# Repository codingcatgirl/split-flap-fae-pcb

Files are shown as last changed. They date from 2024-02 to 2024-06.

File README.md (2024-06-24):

# Split-Flap Fae PCB

This repository contains an alternative, improved, (near) drop-in replacement PCB for [David Kingsman's Split-Flap Display](https://github.com/Dave19171/split-flap). 

**Please note** that due to some changes in pinout, you need to use [evilscientress' improved fork of the firmware](https://github.com/evilscientress/split-flap), which was specifically created along with this PCB.

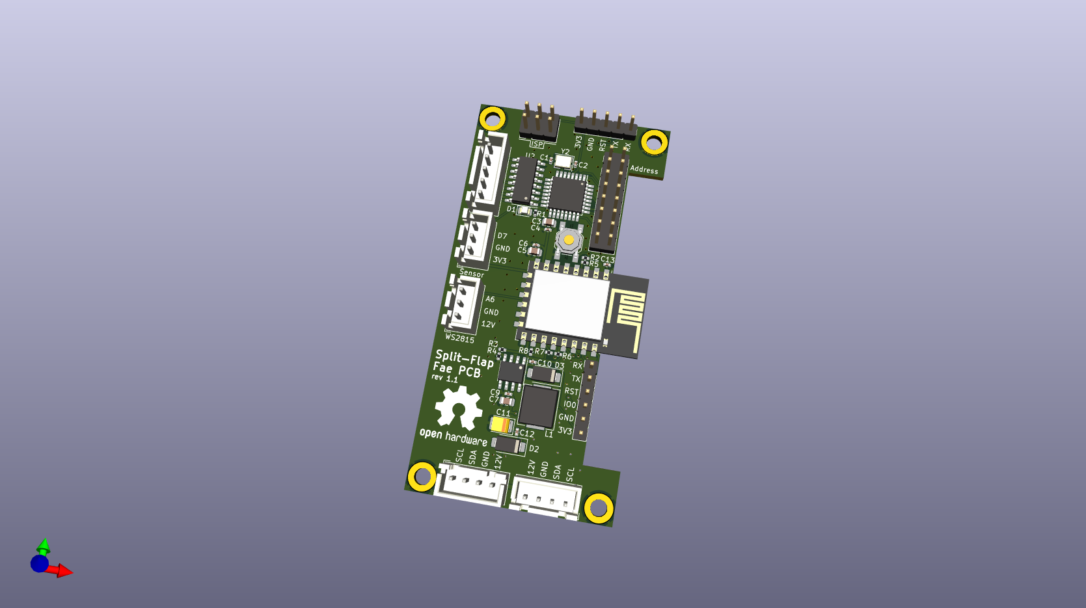
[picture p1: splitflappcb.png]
3D rendering of the PCB


It provides the following Features:

- Identical PCB outline, connectors and connector positions.
- Removed Arduino Nano, use its Atmega328P directly, saving cost and space.
- Run the Atmega328P on 3V3, removing the need for a 5V rail and logic conversion and increasing power efficiency by using a step-down converter (TPS5430). The entire assembly runs on 3V3 logic now.
- Removed the ESP-12F module and use its ESP8266 chip directly, simplifying the PCB again.
- Added ISP and Serial headers to flash both chips.
- Added more jumpers for address configuration, so displays with more than 16 modules could be built in theory, if the firmware supports it.
- Added an additional connector that could be used to connect WS2815 (12V) LED strip.
- Full compatibility with JLCPCB's SMT assembly service.

## How to order the PCBs:
- Use the gerber files in the `fab` folder for the PCB.
- Use the BOM and top-pos files in the `fab` folder for assembly.
- **Deselect assembly for the ESP2866 module, since you need it on one PCB only. You should solder it on yourself.**
  - To omit the ESP2866 module, deselect U4.
  - To omit the serial pin header for the ESP2866 module, deselect J8.
  - Other parts that are also only needed for the ESP2866 are R5, R6, R7, R8, C5, and C6. However, since these are very tedious to manually solder and having JLCPCB assemble them costs close to nothing, i recommend keeping them in.

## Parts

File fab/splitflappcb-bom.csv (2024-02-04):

Comment | Designator | Footprint | LCSC
22pF | C1,C2 | Capacitor_SMD:C_0402_1005Metric | C1555
220uF | C11 | Capacitor_Tantalum_SMD:CP_EIA-3528-21_Kemet-B | C79111
10uF | C3,C5,C7 | Capacitor_SMD:C_0805_2012Metric | C440198
100n | C4,C6,C9,C10,C12,C13 | Capacitor_SMD:C_0402_1005Metric | C307331
LED | D1 | LED_SMD:LED_0805_2012Metric | C2297
SS54 | D2,D3 | Diode_SMD:D_SMA | C22452
Conn_01x04_Pin | J1,J2 | Connector_JST:JST_XH_B4B-XH-AM_1x04_P2.50mm_Vertical | C161871
Conn_01x05_Pin | J3 | Connector_JST:JST_XH_B5B-XH-AM_1x05_P2.50mm_Vertical | C161872
AddressJumpers | J4 | Connector_PinHeader_2.54mm:PinHeader_2x08_P2.54mm_Vertical | C492425
HallSensor | J5 | Connector_JST:JST_XH_B3B-XH-AM_1x03_P2.50mm_Vertical | C144394
AVR-ISP-6 | J6 | Connector_PinHeader_2.54mm:PinHeader_2x03_P2.54mm_Vertical | C65114
Serial-328P | J7 | Connector_PinHeader_2.54mm:PinHeader_1x05_P2.54mm_Vertical | C492404
Serial-ESP12E | J8 | Connector_PinHeader_2.54mm:PinHeader_1x06_P2.54mm_Vertical | C37208
WS2815 | J9 | Connector_JST:JST_XH_B3B-XH-AM_1x03_P2.50mm_Vertical | C144394
47uH | L1 | Inductor_SMD:L_Chilisin_BMRx00060630 | C475913
220 | R1 | Resistor_SMD:R_0402_1005Metric | C25091
10k | R2,R3,R5,R6,R7,R8 | Resistor_SMD:R_0402_1005Metric | C25744
5k9 | R4 | Resistor_SMD:R_0402_1005Metric | C273691
RESET | SW1 | Button_Switch_SMD:SW_SPST_SKQG_WithStem | C318884
TPS5430 | U1 | Package_SO:SOIC-8-1EP_3.9x4.9mm_P1.27mm_EP2.514x3.2mm_ThermalVias | C9864
ULN2003A | U2 | Package_SO:SOIC-16_3.9x9.9mm_P1.27mm | C7512
ATmega328P-A | U3 | Package_QFP:TQFP-32_7x7mm_P0.8mm | C14877
ESP-12E | U4 | RF_Module:ESP-12E | C89297
16MHz | Y2 | Crystal:Crystal_SMD_3225-4Pin_3.2x2.5mm | C13738

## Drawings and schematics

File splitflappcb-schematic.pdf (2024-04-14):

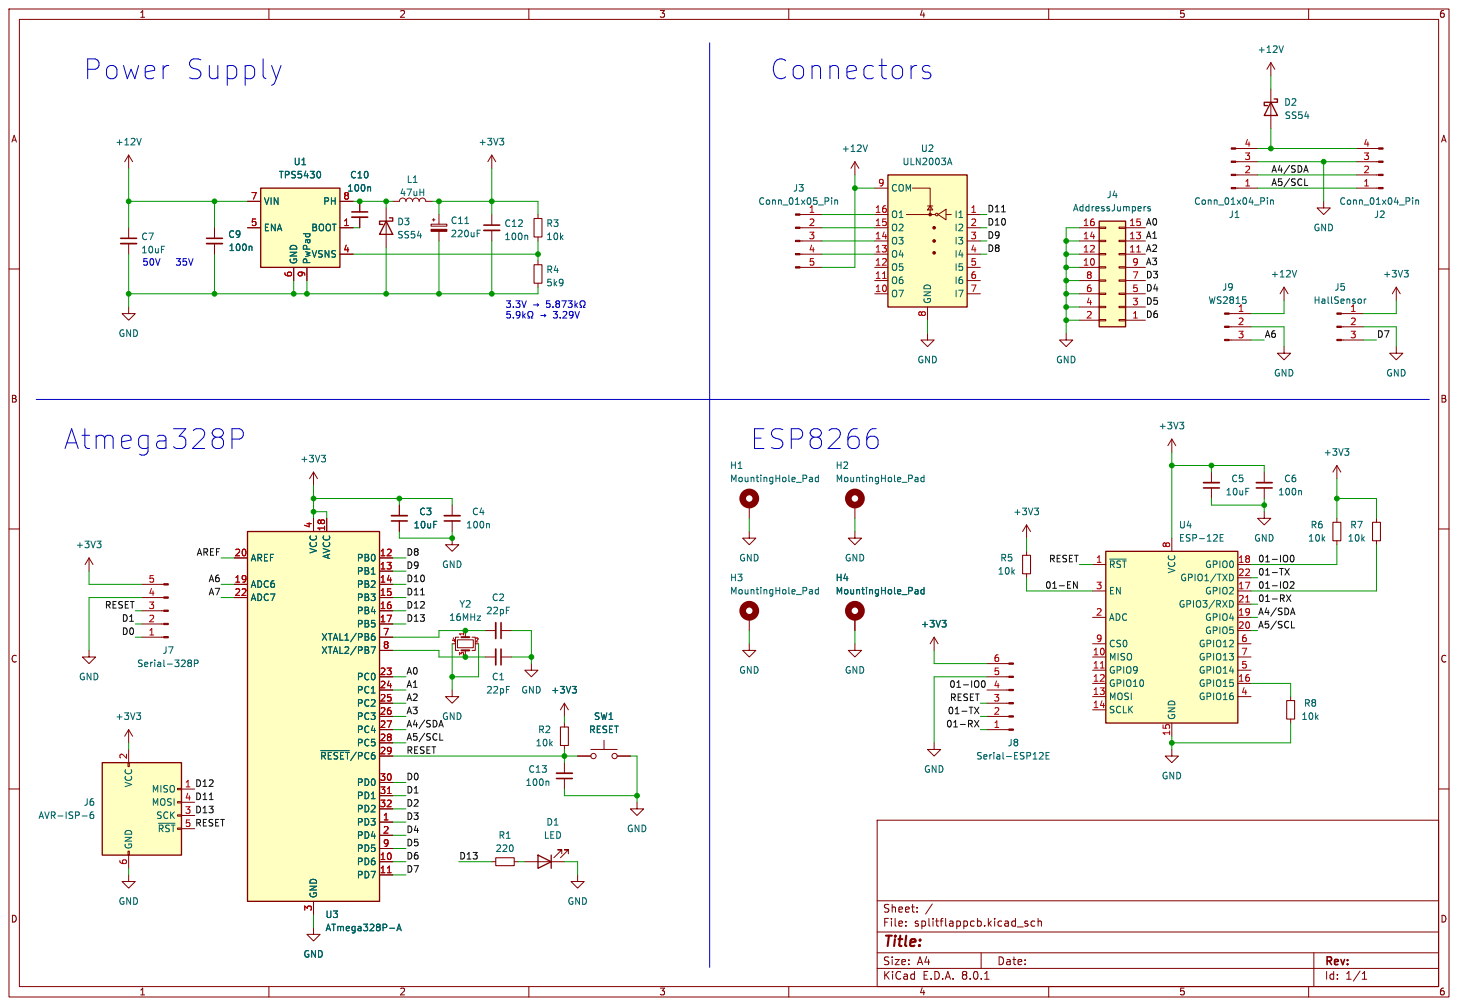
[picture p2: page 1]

þÿ5.9k©þÿ!’3.29V Power Supply

2 SCK 3 MOSI 4 ~{RST}5 GND

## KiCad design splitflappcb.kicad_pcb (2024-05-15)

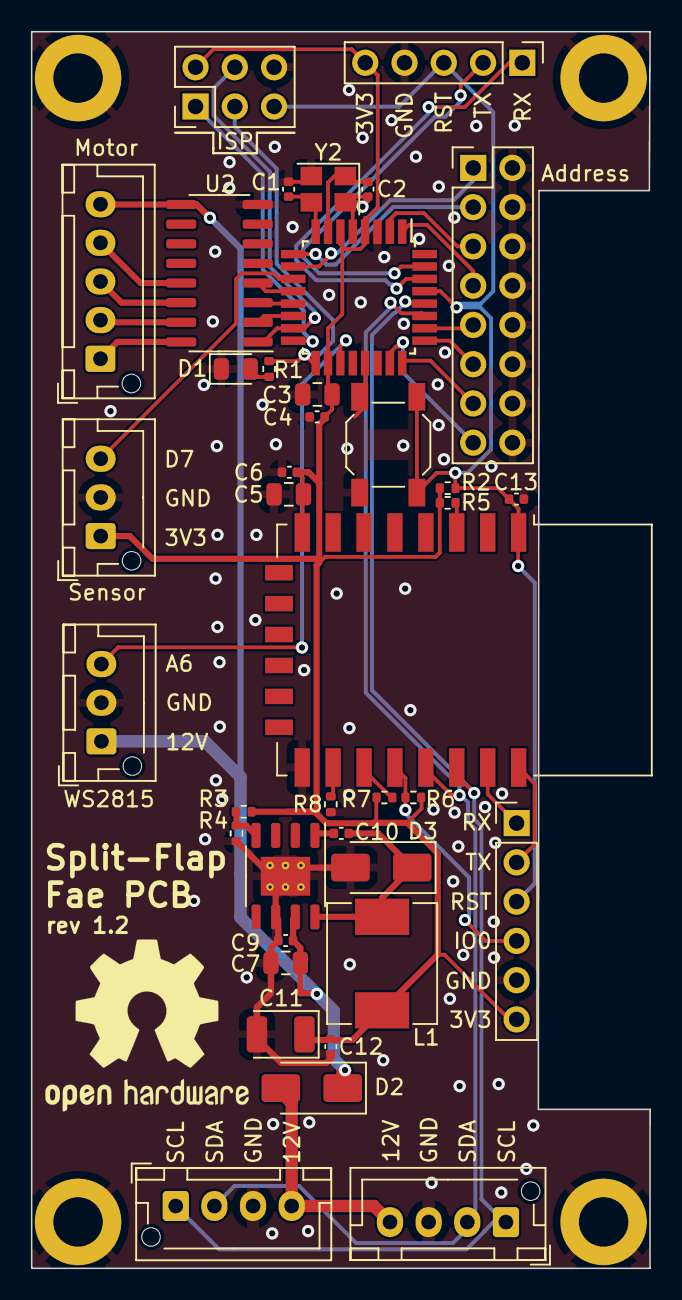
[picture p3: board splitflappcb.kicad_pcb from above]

Board: 2 copper layers, 40.0 x 80.0 mm, 43 parts (0 on the bottom side), 41 nets.

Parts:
C1, C2: 22pF; C_0402_1005Metric
C3, C5, C7: 10uF; C_0805_2012Metric
C4, C6, C9, C10, C12, C13: 100n; C_0402_1005Metric
C11: 220uF; CP_EIA-3528-21_Kemet-B
D1: LED; LED_0805_2012Metric
D2, D3: SS54; D_SMA
H1, H2, H3, H4: MountingHole_Pad; MountingHole_3.2mm_M3_DIN965_Pad
J1, J2: Conn_01x04_Pin; JST_XH_B4B-XH-AM_1x04_P2.50mm_Vertical
J3: Conn_01x05_Pin; JST_XH_B5B-XH-AM_1x05_P2.50mm_Vertical
J4: AddressJumpers; PinHeader_2x08_P2.54mm_Vertical
J5: HallSensor; JST_XH_B3B-XH-AM_1x03_P2.50mm_Vertical
J6: AVR-ISP-6; PinHeader_2x03_P2.54mm_Vertical
J7: Serial-328P; PinHeader_1x05_P2.54mm_Vertical
J8: Serial-ESP12E; PinHeader_1x06_P2.54mm_Vertical
J9: WS2815; JST_XH_B3B-XH-AM_1x03_P2.50mm_Vertical
L1: 47uH; L_Chilisin_BMRx00060630
R1: 220; R_0402_1005Metric
R2, R3, R5, R6, R7, R8: 10k; R_0402_1005Metric
R4: 5k9; R_0402_1005Metric
SW1: RESET; SW_SPST_SKQG_WithStem
U1: TPS5430; SOIC-8-1EP_3.9x4.9mm_P1.27mm_EP2.514x3.2mm_ThermalVias
U2: ULN2003A; SOIC-16_3.9x9.9mm_P1.27mm
U3: ATmega328P-A; TQFP-32_7x7mm_P0.8mm
U4: ESP-12E
Y2: 16MHz; Crystal_SMD_3225-4Pin_3.2x2.5mm

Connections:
+3V3: C3.2, C4.2, C5.2, C6.2, C11.1, C12.1, J5.1, J6.2 (VCC), J7.5, J8.6, L1.2, R2.1, R3.1, R5.1, R6.1, R7.1, U3.4 (VCC), U3.6 (VCC), U3.18 (AVCC), U4.8 (VCC)
+12V: C7.1, C9.1, D2.1 (K), J3.5, J9.1, U1.7 (VIN), U2.9 (COM)
/01-EN: R5.2, U4.3 (EN)
/01-IO0: J8.4, R6.2, U4.18 (GPIO0)
/01-IO2: R7.2, U4.17 (GPIO2)
/01-RX: J8.1, U4.21 (GPIO3/RXD)
/01-TX: J8.2, U4.22 (GPIO1/TXD)
/A0: J4.15, U3.23 (PC0)
/A1: J4.13, U3.24 (PC1)
/A2: J4.11, U3.25 (PC2)
/A3: J4.9, U3.26 (PC3)
/A4/SDA: J1.2, J2.2, U3.27 (PC4), U4.19 (GPIO4)
/A5/SCL: J1.1, J2.1, U3.28 (PC5), U4.20 (GPIO5)
/A6: J9.3, U3.19 (ADC6)
/D0: J7.1, U3.30 (PD0)
/D1: J7.2, U3.31 (PD1)
/D3: J4.7, U3.1 (PD3)
/D4: J4.5, U3.2 (PD4)
/D5: J4.3, U3.9 (PD5)
/D6: J4.1, U3.10 (PD6)
/D7: J5.3, U3.11 (PD7)
/D8: U2.4 (I4), U3.12 (PB0)
/D9: U2.3 (I3), U3.13 (PB1)
/D10: U2.2 (I2), U3.14 (PB2)
/D11: J6.4 (MOSI), U2.1 (I1), U3.15 (PB3)
/D12: J6.1 (MISO), U3.16 (PB4)
/D13: J6.3 (SCK), R1.2, U3.17 (PB5)
/RESET: C13.2, J6.5 (~RST), J7.3, J8.3, R2.2, SW1.1, U3.29 (~RESET/PC6), U4.1 (~RST)
GND: C1.1, C2.1, C3.1, C4.1, C5.1, C6.1, C7.2, C9.2, C11.2, C12.2, C13.1, D1.1 (K), D3.2 (A), H1.1, H2.1, H3.1, H4.1, J1.3, J2.3, J4.2, J4.4, J4.6, J4.8, J4.10, J4.12, J4.14, J4.16, J5.2, J6.6 (GND), J7.4, J8.5, J9.2, R4.2, R8.2, SW1.2, U1.6 (GND), U1.9 (PwPad), U2.8 (GND), U3.3 (GND), U3.5 (GND), U3.21 (GND), U4.15 (GND), Y2.2, Y2.4
unnamed: D1.2 (A), R1.1
unnamed: D2.2 (A), J1.4, J2.4
unnamed: C10.1, D3.1 (K), L1.1, U1.8 (PH)
unnamed: J3.1, U2.16 (O1)
unnamed: J3.2, U2.15 (O2)
unnamed: J3.3, U2.14 (O3)
unnamed: J3.4, U2.13 (O4)
unnamed: C10.2, U1.1 (BOOT)
unnamed: R3.2, R4.1, U1.4 (VSNS)
unnamed: C2.2, U3.7 (XTAL1/PB6), Y2.1
unnamed: C1.2, U3.8 (XTAL2/PB7), Y2.3
unnamed: R8.1, U4.16 (GPIO15)

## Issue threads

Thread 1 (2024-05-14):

SCK and MOSI pins swapped

turtlekiosk, 2024-05-14:
Hi, this is a great design and I got it fabbed at JLC. I was trying to program the atmega using the ISP pins and I noticed the MOSI and SCK pins are swapped on the board!

codingcatgirl, 2024-05-15:
What do you mean, "swapped"? Are they labeled incorrectly? That's not been the case when i flashed them.

So i assume you just have a programmer that has a 6-pin connector for the ISP headers and those two pins are swapped on it? That's unfortunate then, but would indicate that your programmer probably just uses a non-standard layout?

turtlekiosk, 2024-05-15:
Ah sorry, you're right, the actual pinout is correct. I didn't notice because I was using an Arduino as ISP to flash the chips so I was manually inserting the leads into each pin, but I do think the labels for SCK and MOSI are labeled incorrectly.

evilscientress, 2024-05-15:
btw. @turtlekiosk  The original firmware is not compatible with this PCB. I have a fork that works with the PCB we designed and also has some additional functionality.
https://github.com/evilscientress/split-flap

btaylor112, 2024-06-23:
@evilscientress Sorry to clarify, is the firmware you have updated compatible with this updated PCB?

evilscientress, 2024-06-24:
@btaylor112 yes. @codingcatgirl and me designed the PCB together. The firmware was modified specifically for this PCB.

Closed 2024-05-15.

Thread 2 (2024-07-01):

Adress Jumper

JoeBerlin69, 2024-07-01:
How do I use these adress jumpers? From top or bottom?
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

btaylor112, 2024-07-06:
Have you managed to resolve this? I'm having a similar issue, I'm not sure how they address?

JoeBerlin69, 2024-07-06:
I am sorry. No i haven't a solution. I took some original pcbs from david. They work well. A built 10 split flaps in the past. They all work well. This was my first attempt (and really expensive) with this pcb and i hope, s.o. can help me with my problems told in my second issue.

codingcatgirl, 2024-07-07:
Hey, all pins are labeled on the back of the PCB:
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

The source code of @evilscientress' fork states:

```c
#define ADRESSSW1 6
#define ADRESSSW2 5
#define ADRESSSW3 4
#define ADRESSSW4 3
```

Meaning tht only the top 4 jumpers currently control the address, in that order. The other jumpers can be used for something else or for more address bits in the future.

btaylor112, 2024-07-07:
Sorry if this is a silly question - Do I use the jumpers like this?

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

codingcatgirl, 2024-07-07:
Those are precisely the wrong ones. You gotta use the top ones. The bottom ones are unused for now.

btaylor112, 2024-07-07:
Like this?
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

codingcatgirl, 2024-07-07:
I'm on my way right now and can't verify it. Please just… try it out?

jvdhoeven, 2024-07-11:
I had the same issue. After some debugging I found that you have to uncomment [this](https://github.com/evilscientress/split-flap/blob/5f9a4b5b43410703144f7017ba2156e04885de44/ESPMaster/ESPMaster.ino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) line. After uploading the new firmware it was working. On the ESPMaster board you just leave the address blank (no jumpers). Hope this helps!

joachimklug, 2024-11-09:
Quite late to the party but wanted to clarify as others might stumble over it:

Checking the `Unit.ino` file it states:
```C++
// Pins of I2C adress switch
#define ADRESSSW1 6
#define ADRESSSW2 5
#define ADRESSSW3 4
#define ADRESSSW4 3
```

The function `getaddress` then translates the jumpers into the address and returns it
```C++
//returns the adress of the unit as int from 0-15
int getaddress() {
  int address = !digitalRead(ADRESSSW4) + (!digitalRead(ADRESSSW3) * 2) + (!digitalRead(ADRESSSW2) * 4) + (!digitalRead(ADRESSSW1) * 8);
  return address;
}
```

This means jumpers need to be set like this:
|  | D6 | D5 | D4 | D3 |
|---|---|---|---|---|
| Unit 1 (Master) |  |  |  |  |
| Unit 2 |  |  |  | x |
| Unit 3 |  |  | x |  |
| Unit 4 |  |  | x | x |
| Unit 5 |  | x |  |  |
| Unit 6 |  | x |  | x |
| Unit 7 |  | x | x |  |
| Unit 8 |  | x | x | x |
| Unit 9 | x |  |  |  |
| Unit 10 | x |  |  | x |

Or in picture. This is the setting for Units 1-4
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

For my liking it is not obvious to start in the middle to set the jumpers. However when someone reads the code is it quite clear :)
I will most probably adapt my `getaddress()` function to calculate it the other way around. One could do it via the `ADRESSSW` definitions but for me `1` sounds like the lowest bit.

Thanks a lot for this great PCB design!

Closed 2024-07-07.

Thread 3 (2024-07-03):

Flash Problems after ESP soldered on

JoeBerlin69, 2024-07-03:
Hello, the boards made by JLPCB cannot be flashed if an ESP is soldered on. If both parts are separated, flashing works perfectly. When I uploaded the layout to JLPCB, there were problems with the arrangement of the components. I had to position many of them manually and, above all, rotate them. It is possible that I did something wrong here. Are you aware of similar problems? The units seem to work without ESP, so at least they rotate when power is applied and stop at the right place. Best regards

codingcatgirl, 2024-07-03:
Just like the original PCB only has the ESP-01 on one PCB, you only need the ESP on one of these PCBs as well.

You should have read the readme, which states so clearly in **bold text**.

> **Deselect assembly for the ESP2866 module, since you need it on one PCB only. You should solder it on yourself.**

JLCPCB not showing the components in the correct roation in the preview is normal and can be ignored, as they also write next to the preview.

JoeBerlin69, 2024-07-03:
Thank you for your quick reply. I also ordered and received the boards without the ESP. My problem is that after soldering on the ESP I can no longer establish a serial connection to either the ATmega or the ESP. I also don't know how to jumper the address bar. Perhaps you also know the problem with the serial connection.

codingcatgirl, 2024-07-07:
The most likely explanation for this is simply that didn't solder it on right. It can be a bit tricky and, but if the entire board doesn't work that would indicate a short.

evilscientress, 2024-07-07:
If both the ESP and the AVR don't respond anymore my guess is an issue with the RESET bus. Both MCUs have their RESET inputs connected. The line should have 3.3V.

JoeBerlin69, 2024-07-07:
I will check it again. Funfact: i soldered 2 PCBs with an ESP. Both show exactly the same wrong behavior.
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

codingcatgirl, 2024-07-07:
Maybe the i'm not seeing it right, but this looks like you are using way too much solder, which can easily cause shorts somewhere. You should check using a multimeter.

codingcatgirl, 2024-07-07:
Maybe the i'm not seeing it right, but this looks like you are using way too much solder, which can easily cause shorts somewhere. You should check using a multimeter.

JoeBerlin69, 2024-07-07:
I tested it with the multimeter and couldn't find a short of neighboured pins. I also checked the connection of the serial pinout and the Pins. That seems fine. But I will next week check the parameters of my programmer. In the past i had some problems with them. The serial output was rubbish.
I can flash both chips without any problems if they're separated.
I will continue testing next week. Thanks a lot for your help.
Joerg

jvdhoeven, 2024-07-11:
Maybe it helps: I was able to flash the atmega via the ISP pins using an arduino uno as programmer. I was unable to do it via the serial connections/pins on the bottom right, but did not investigate further. Flashing the ESP worked with no issue.

evilscientress, 2024-07-11:
Yes you have to use ISP to burn the bootloader then you can use serial. That is normal. A AVR from the factory has no support for serial programming. You **have** to use ISP first and set the right fuses.

jonbloom, 2024-07-18:
I believe I flashed the bootloader via ISP succussfully, as now the board blinks green when applying power. Having said that, when connecting via the serial header (RX/TX/GND) toward the top of the board, I haven't had luck programming. I'm using a USB-TTL adapter on my Mac, which I have used elsewhere successfully. Basically just getting this error repeatedly:
```
avrdude: stk500_recv(): programmer is not responding
avrdude: stk500_getsync() attempt 1 of 10: not in sync: resp=0x00
```

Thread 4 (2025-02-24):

Positions not rendering correctly at JLCPCB

d-alberts, 2025-02-24:
Positions and rotations for components are not rendering correctly for me at JLCPCB. I'm not familiar enough with the files or supplier to differentiate between a rendering problem and actual problem.

I am uploading
* Gerber (PCB): the entire (zipped) fab folder
* BOM (assembly): splitflap-bom.csv
* CPL (assembly): splitflap-top-pos.csv

J1, J2 are out of stock; that's unrelated to any BoM or placement issue.

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

codingcatgirl, 2025-02-24:
This is not an issue, they orient them correctly later.

For J1 and J2, any other pin header that fits the footprint can be used, of course – or you can hand-solder it.

Closed 2025-02-24.

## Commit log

2024-02-04 update to rev1.1
    [pcb BOM.csv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]
2024-04-14 add schematic and pcb rendering, remove empty csv
    [splitflappcb-bottom-pos.csv]
2024-05-15 rev 1.2 – fix incorrect pin labels on ISP connector (fixes #1)
    [splitflappcb-B_Cu.gbl, splitflappcb-B_Mask.gbs, splitflappcb-B_Paste.gbp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]
